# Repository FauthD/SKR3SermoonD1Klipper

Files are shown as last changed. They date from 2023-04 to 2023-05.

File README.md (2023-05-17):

# SKR3SermoonD1Klipper
Klipper settings for BTT SKR3 built into the Creality Sermoon D1

## Status
Printer works fine and I think not much will come anymore from my side.
The reason is that I switch to another board (MKS Monster8). It is not the fault of the SKR3 board which is a very fine board with very good documentation and a fair price.

However I want to add an auxilary feeder (extruder) that ensures the filament gets feed correctly into the direct extruder. Currently I sometimes have issues with material transport and get under extrusion. For that extra stepper motor it needs an extra driver, one too much for the SKR3. Yes, there is the Ext-M board that can extend the SKR3 with 3 more axes. I even created a mounting holder that can carry an EXT board. Unfortunatelly none of the stores I checked (many!) could deliver this board with reasonable delivery time. Since I can re-use the SKR3 in another project, I decided to go with a board with at least one more axis. The MKS Monster8 is small enough to fit easily underneath the fan. (The Octopus board is quite a bit wider).
Find my repo for the Monster8 here: https://github.com/FauthD/MksMonster8V2SermoonD1Klipper .

## Mechanics
Created an adapter to mount the SKR 3 since it does not fit to the mounting holes in the Sermnoon D1. Later I added some mounts for a big 120mm fan (because it was easier with a fan larger than the board). The fan runs with about 600 rmp and is barly audible.

Since I planed to add an extra stepper for a auxilary feeder, some space for the BTT Exp board was neccessary. Find the .stl and .scad files in directory SKR3-Adapter and below.

| No fan | 120mm fan | 120mm fan + ext board |
| :----: | :----: | :----: |
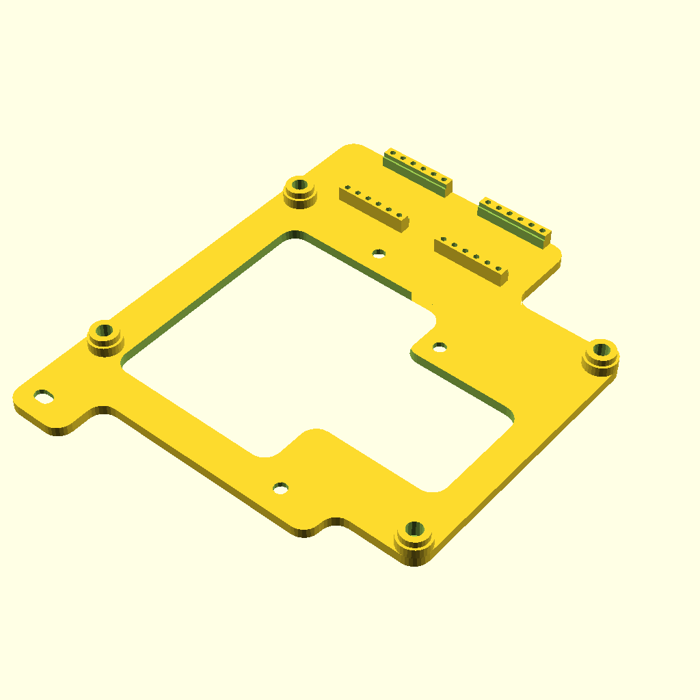
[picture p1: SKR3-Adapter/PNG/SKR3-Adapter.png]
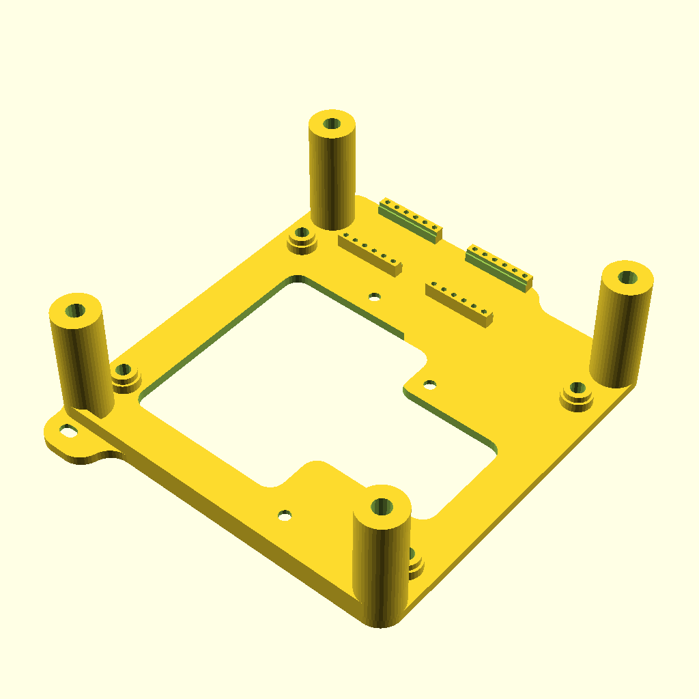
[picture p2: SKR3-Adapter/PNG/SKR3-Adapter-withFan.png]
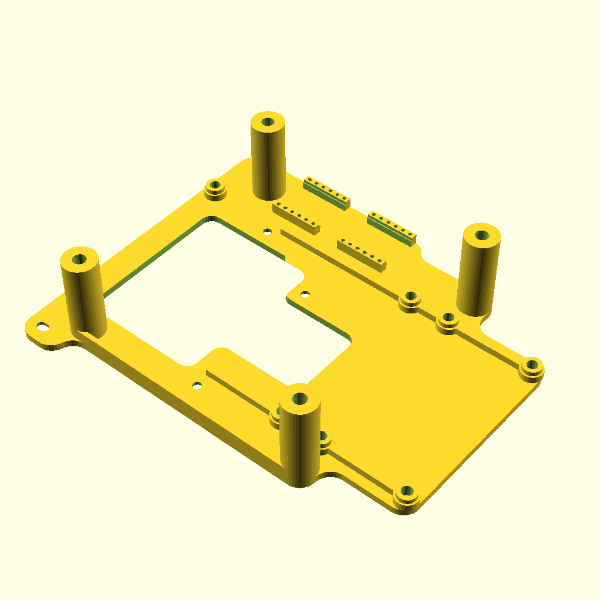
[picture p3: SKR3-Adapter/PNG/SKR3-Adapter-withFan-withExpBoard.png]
|  |  | 

Note: You either need to cut a hole onto the bottom sheet or replace it with some new bottom and larger feet. (Due to the board change I will not design a new bottom sheet for this board.)

Note2: The original mainboard fan does not transport much air, but makes quite some noise. So a slow turning 120mm fan running at 7V is much better.
The next source of noise is the fan in the power supply. I replaced that fan with a low noise 120mm fan running from 12V. Now it is barly audible and still produces a much better airflow. PSU stays cool even for long prints.
Both the 12V and the 7V are generated by cheap (0.7€+shipping) step down regulators. They are mounted onto the adapter.

Note3: We need heigher feet. Already printed some test feet with 28mm height (need 40mm screws - probably will increase by 5mm when I have that screws available).

Note4: I cannot check whether the original wires are long enough since I did buy the printer used and the wires are not original anymore.

### Rebuilding the .stl files
You need openscad installed.

On Linux, navigate into the directory SKR3-Adapter, open a cmd line and run make.

On Windows you also need some version of gmake installed. I do not use Windows anmore, so you are on your own.

### Photos:

| Adapter | Mainboard | Step down regulators | Total |
| :----: | :----: | :----: | :----: |
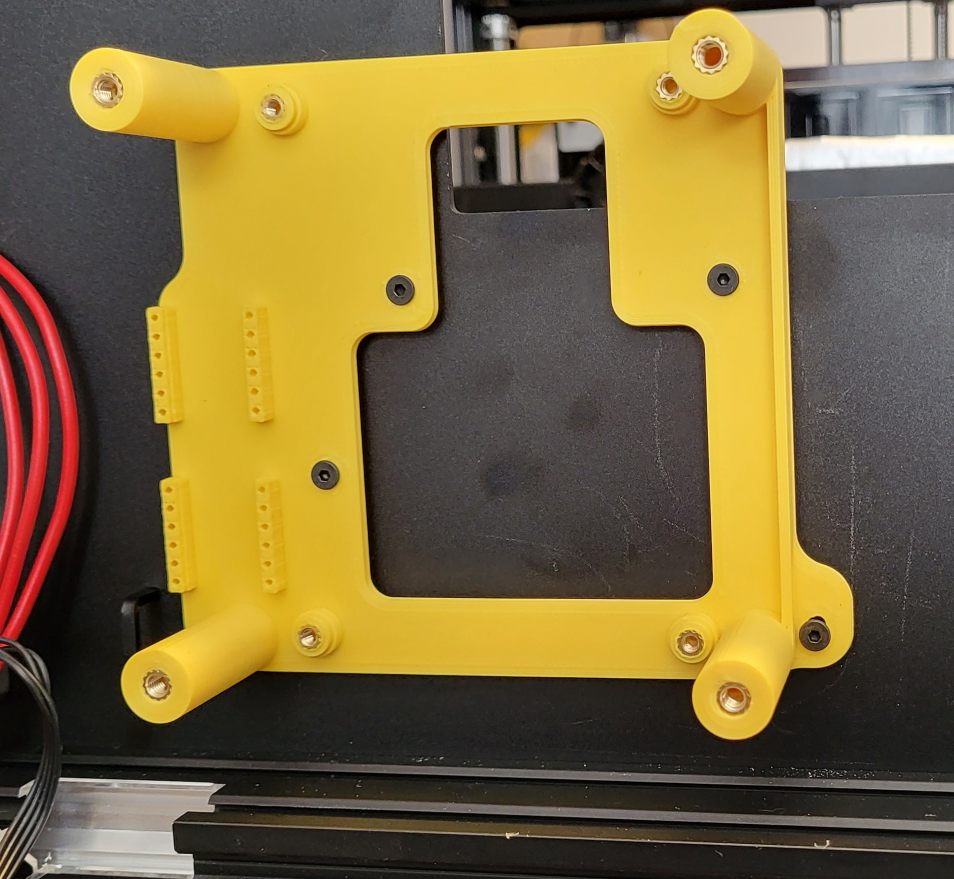
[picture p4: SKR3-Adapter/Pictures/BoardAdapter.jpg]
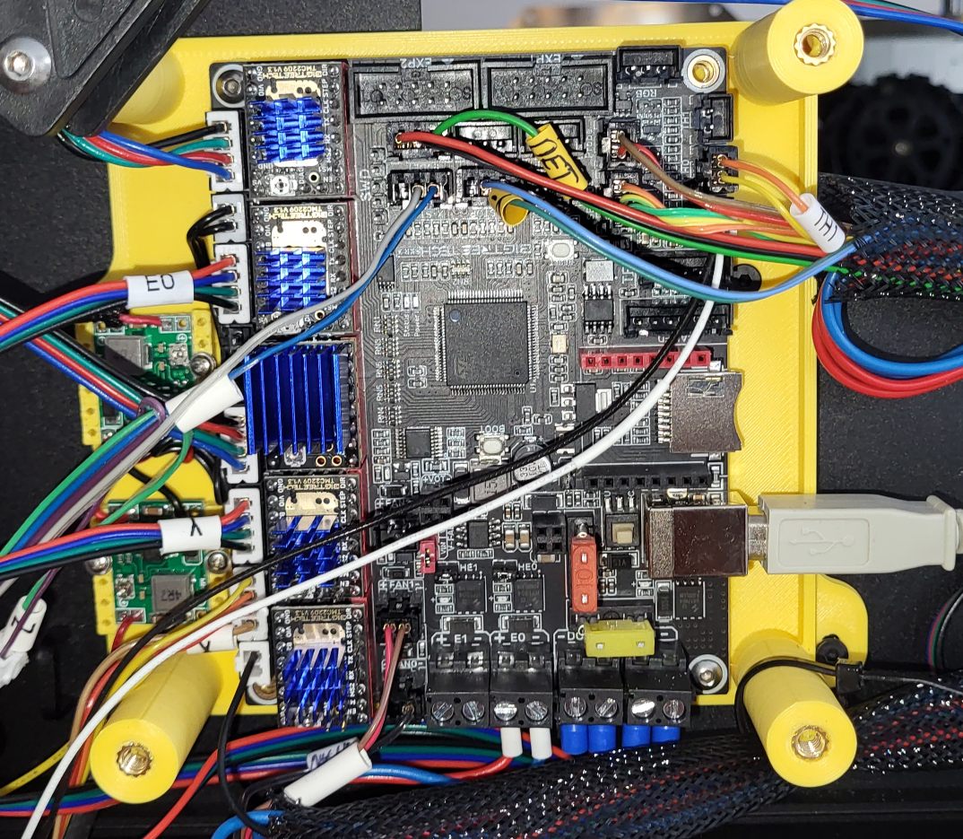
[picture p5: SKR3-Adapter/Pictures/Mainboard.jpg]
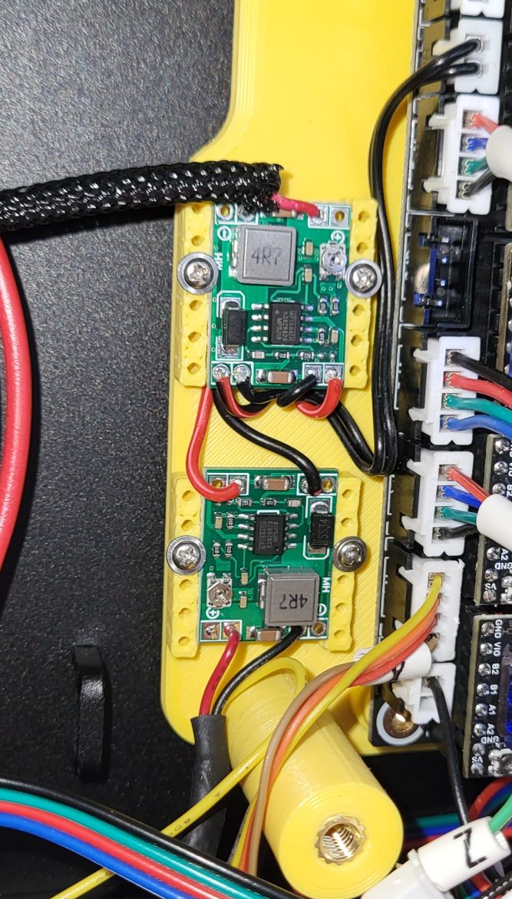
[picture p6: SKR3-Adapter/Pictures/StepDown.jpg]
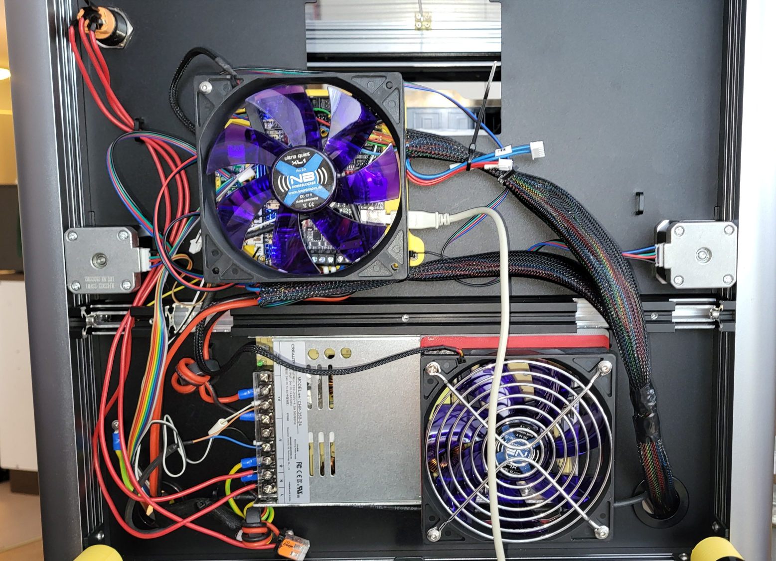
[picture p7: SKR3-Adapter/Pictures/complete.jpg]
|  |  |  |  |

## Klipper
Installed MainsaleOS on a RPi, created the firmware and flashed.
X and Y axis work including the limit switches.

CR Touch is working fine.
Even the Z-Tilt option works very nice.
Z Axis is much more silent (one reason I did all this, the original drivers for Z are very noisy).

X and Y axis have some resonances when they move fast. Turning stealthchop on reduced the resonances a lot.

Extruder works and is calibrated.

Bed mesh works (I am not happy with my bed yet).

A test with a LED RGB ring was succesful, but this is merly an example.

Note: I had issues with the Z axes (suddenly lots of noise, intermediatly running in wrong direction). To hunt this I added an extra SKR 3 E3 mini board for the Z Axes (Klipper is so flexible).

At the end it turned out that the (new) cables to the steppers are faulty and provided not always a good contact. After replacing these, all was fine.

Now I am back to the SKR 3 only, but the extra lines for the Mini 3E are still there as comments.

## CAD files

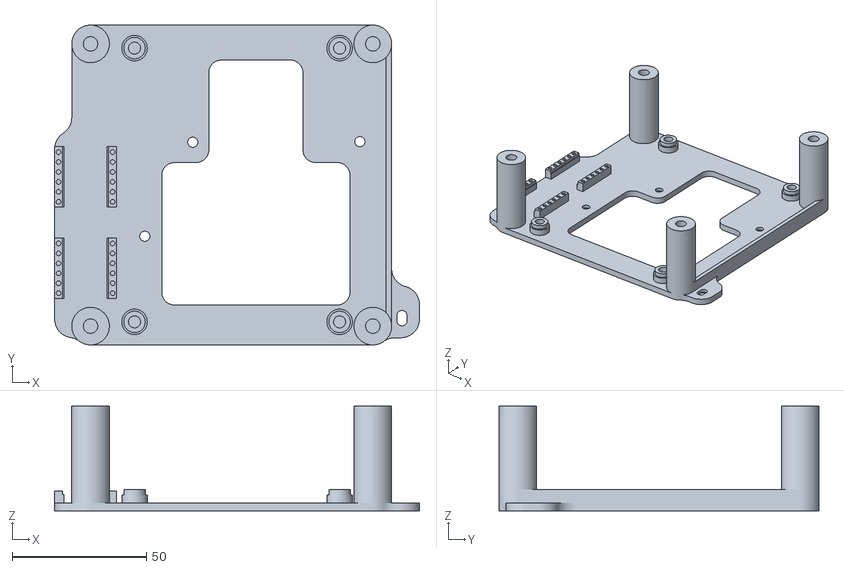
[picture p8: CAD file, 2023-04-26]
SKR3-Adapter/STL/SKR3-Adapter-withFan.stl
135.8 x 119.0 x 39.0

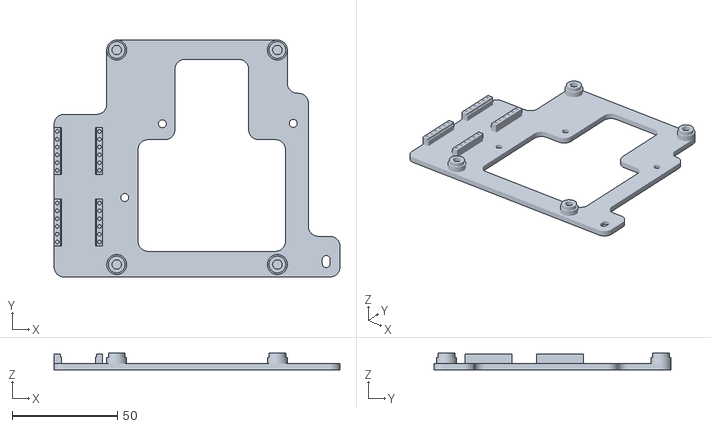
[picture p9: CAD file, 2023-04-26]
SKR3-Adapter/STL/SKR3-Adapter.stl
135.8 x 112.5 x 8.00

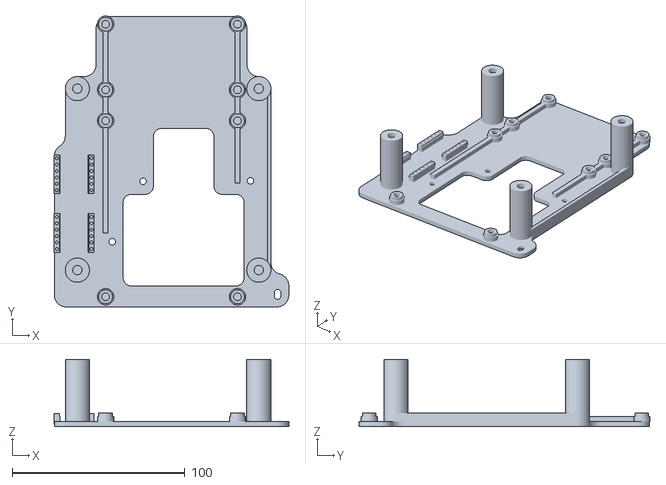
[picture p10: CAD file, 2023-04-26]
SKR3-Adapter/STL/SKR3-Adapter-withFan-withExpBoard.stl
135.8 x 168.4 x 39.0

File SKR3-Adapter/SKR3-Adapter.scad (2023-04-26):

// An adapter to mount the BTT SKR3 board into Creality mounting holes.
// Aimed for the Sermoon D1.
// The SKR3 is mounted 90° compared to the Creality board.
// This way the cables fit in lenght and there is enough room for the USB connector.
// For mounting you need 4 * M3 heat inserts (OD=5mm, l=4mm).
// I recommend to replace the original screws from the old board with ones with a flatter head.
//
// Copyright (C) 2023 Dieter Fauth
// This program is free software: you can redistribute it and/or modify it under the terms of the GNU General Public License as published by the Free Software Foundation, either version 3 of the License, or (at your option) any later version.
// This program is distributed in the hope that it will be useful, but WITHOUT ANY WARRANTY; without even the implied warranty of MERCHANTABILITY or FITNESS FOR A PARTICULAR PURPOSE. See the GNU General Public License for more details. You should have received a copy of the GNU General Public License along with this program. If not, see <http://www.gnu.org/licenses/>.
// Contact: dieter.fauth at web.de

/* [Print] */

PrintThis = "all"; // ["all", "mount"]

/* [Board Sizes] */
BoardLenght=109.7;
BoardWidth=84.3;

DrillLenght=101.85;
DrillWidth=76.3;
CrealityDrillDiameter=3.8;
// For M3 heat inserts use 4.5 else 2.5.
SkrDrillDiameter=4.5;
MountDiameter=9.5;

MountDistance=25;
MountHeight=5;
Thickness=3;

// Move SKR3 to the left
Offset_X=12;
// Move SKR3 to upper
Offset_Y=16;

/* [Options] */
UseFan=true;
FanDiameter=120;
FanScrewDistance=105;
// For M4 heat inserts use 5.4 else 3.5.
FanScrewDiameters=5.4;
FanMountingPostDiameter=14;
FanHeight=36;
// Move Fan to the left
FanOffset_X=2;

/* [EXP-Board] */
UseExpBoard=true;
ExpDistance=2;
ExpBoardLenght=46.0;
ExpDrillLenght=38.0;

/* [Hidden] */

module __Customizer_Limit__ () {}
    shown_by_customizer = false;

$fa = $preview ? 2 : 0.5;
$fs = $preview ? 1 : 0.5;

// If you enable the next line, the $fa and $fs are ignored.
// $fn = $preview ? 12 : 100;
Epsilon = 0.01;
epsilon = Epsilon;

/* Creality holes */
// These are relative to the lower left corner of the board.
// I took them from the BTT E3 Mini board.
// https://github.com/bigtreetech/BIGTREETECH-SKR-mini-E3/blob/master/hardware/BTT%20SKR%20MINI%20E3%20V3.0.1/Hardware/BTT%20E3%20SKR%20MINI%20V3.0.1_SIZE.pdf

E3Mini=[103.75, 70.25];

UnkownDifference=-1.0;  // one hole was not correct, empiric fix with a slotted hole

Drill1=[23.4,67.03, 0];
Drill2=[85.55, E3Mini.y-3.02, 0];
Drill3=[5.54, 32.05, 0];
Drill4=[37.34, 29.41, 0];
Drill5=[101.22, 2.56, 0];

Rounding=MountDiameter/2;

FanOffset_Y=UseExpBoard ? 17 : 0;
Enlarge=1.5;

///////////////////////////////////////////////////////////////////////////////
// Some helpers to round combined objects
module RoundConvex(r)
{
	offset(r = r)
	{
		offset(delta = -r)
		{
			children();
		}
	}
}

module RoundConcave(r)
{
	offset(r = -r)
	{
		offset(delta = r)
		{
			children();
		}
	}
}

module RoundThis(r)
{
	RoundConcave(r) RoundConvex(r) children();
}

// Can round combined 2D objects and make them 3D
module RoundExtrude(r, h)
{
	linear_extrude(height = h)
		RoundThis(r) children();
}

///////////////////////////////////////////////////////////////////////////////
// long hole
module SlottedHole(d, h, length)
{
   translate([0, 0, h/2])
      cube(size=[length, d, h+Epsilon], center=true);
      
   for(x=[-length/2,length/2])
   {
      translate([x, 0, h/2])
      {
         cylinder(d=d, h=h+Epsilon, center=true);
      }
   }
}

///////////////////////////////////////////////////////////////////////////////
// Helper for mounting step down boards with MP1584EN

module PcbMount(size, pcb)
{
   len=size.x;
   width=size.y+6;
   screw_dia=1.8;

   difference()
   {
      translate([0,0,size.z/2])
         cube([len,width, size.z], center=true);

      translate([0,0,size.z])
         cube([len+Epsilon,size.y, 2*pcb], center=true);

      translate([0,0,size.z/2])
         cube([len+Epsilon,size.y-1, size.z+Epsilon], center=true);

      for(n=[-1,1])
      {
         for(m=[-1:0.4:1])
         {
            translate([m*(len/2-2),n*(width/2-1.5),size.z/2])
               cylinder(d=screw_dia, h=20*size.z, center=true);
         }
      }
   }
}

module StepDown_MP1584EN()
{
   PcbMount(size=[22.5, 17.1, 6], pcb=1.4);
}

///////////////////////////////////////////////////////////////////////////////
// The Fan

module Fan(h=25)
{
   for(a=[45:90:360-Epsilon])
   {
      rotate([0,0,a])
         translate([FanScrewDistance/1.414, 0, 0])
         {
            difference()
            {
               cylinder(d=FanMountingPostDiameter, h=h, center=true);
               translate([0,0,h/2])
                  cylinder(d=FanScrewDiameters, h=h, center=true);
            }
         }
   }
}

///////////////////////////////////////////////////////////////////////////////
// The adapter

module CrealityHoles(d, h=5*Thickness)
{
   translate(Drill1)
      cylinder(d=d, h=h, center=true);
   translate(Drill2)
      cylinder(d=d, h=h, center=true);
   translate(Drill3)
      cylinder(d=d, h=h, center=true);
   translate(Drill4)
      cylinder(d=d, h=h, center=true);
   translate(Drill5)
      cylinder(d=d, h=h, center=true);
// fix some unknown difference in hole position
   translate([0,UnkownDifference,-h/2])
      translate(Drill5)
         rotate([0,0,90])
            SlottedHole(d=d, h=h, length=d/2);
}

module SKR3Holes()
{
      for(x=[-1,1])
      {
         for(y=[-1,1])
         {
            translate([x*DrillLenght/2, y*DrillWidth/2, 0])
               cylinder(d=SkrDrillDiameter, h=10*Thickness);
         }
      }
}

module ExpHoles()
{
      for(x=[-1,1])
      {
         for(y=[-1,1])
         {
            translate([x*ExpDrillLenght/2, y*DrillWidth/2, 0])
               cylinder(d=SkrDrillDiameter, h=10*Thickness);
         }
      }
}

module BasePlate()
{
   r=UseFan ? FanMountingPostDiameter/2 : Rounding;

   RoundExtrude(r, Thickness)
   {
      rotate([0,0,90])
         square([BoardLenght+Enlarge, BoardWidth+Enlarge], center=true);
      x=E3Mini.x+32;
      y=E3Mini.y+7;
      translate([-x/4, y/2-BoardLenght/2-2+FanOffset_Y/2])
         square([x/2, y+FanOffset_Y], center=true);
      translate([x/4-15, y/2-BoardLenght/2+8])
         square([x/2, y], center=true);
      translate([x/4, y/8-BoardLenght/2-2])
         square([x/2, y/4], center=true);
      
      if(UseExpBoard)
      {
         translate([0, BoardWidth+Enlarge])
            square([BoardWidth+2*Enlarge, ExpBoardLenght+2*Enlarge+ExpDistance], center=true);
      }

      if(UseFan)
      {
         size=FanDiameter-1;
         translate([-FanOffset_X, FanOffset_Y])
            square([size, size], center=true);
      }
   }
}

module CoolingHelper()
{
   RoundExtrude(Rounding, 10*Thickness)
   {
      translate([7, 4])
         square([35,85],center=true);

      translate([7, 20-DrillWidth/2])
         square([70,53],center=true);
   }
}

module BoardMounts(l,w)
   {
      for(x=[-1,1])
      {
         for(y=[-1,1])
         {
            translate([x*l/2, y*w/2, MountHeight/2+Thickness])
               cylinder(d=MountDiameter-1.5, h=MountHeight, center=true);
            translate([x*l/2, y*w/2, MountHeight/2+Thickness-1])
               cylinder(d=MountDiameter, h=MountHeight-2, center=true);
         }
      }
   }

module BoardHolder()
{
   BasePlate();
   rotate([0,0,90])
   {
      BoardMounts(DrillLenght, DrillWidth);
      if(UseExpBoard)
      {
         translate([BoardWidth+Enlarge+ExpDistance,0,0])
            BoardMounts(ExpDrillLenght, DrillWidth);
      }
   }
   if(UseExpBoard)
   {
      // enforcing a bit
      w=3;
      h=3;
      // l1=60;
      // translate([-0.7*l1+3, 0.7*l1+5, Thickness+h/2])
      //    rotate([0,0,35])
      //       cube([w, l1, h], center=true);
      l2=ExpBoardLenght+40+ExpDistance;
      translate([DrillWidth/2, l2/2+15, Thickness+h/2])
         cube([w, l2, h], center=true);
      l3=ExpBoardLenght+74+ExpDistance;
      translate([-DrillWidth/2, l3/2-14, Thickness+h/2])
         cube([w, l3, h], center=true);
   }
}

module Adapter()
{
   difference()
   {
      union()
      {
         BoardHolder();
         extra=4.5;
         for(n=[0,-1])
         {
            translate([-E3Mini.x/2-extra, n*34+3+FanOffset_Y, Thickness/2])
               rotate([0,0,90])
                  StepDown_MP1584EN();
         }
      }

      translate([0,0, Thickness])
         rotate([0,0,90])
         {
            SKR3Holes();
            translate([BoardWidth+Enlarge+ExpDistance,0,0])
               ExpHoles();
         }

      translate([-E3Mini.x/2+Offset_X, -E3Mini.y/2-Offset_Y, 0])
         CrealityHoles(CrealityDrillDiameter);
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

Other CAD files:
SKR3-Adapter/STL/withFan_withExpBoard.stl
SKR3-Adapter/STL/withFan.stl
SKR3-DrillingJig/SKR3-DrillingJig.scad

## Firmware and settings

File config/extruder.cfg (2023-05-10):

[extruder]
max_extrude_only_distance: 1000.0
step_pin: PD15
dir_pin: !PD14
enable_pin: !PC7
microsteps: 16
# after calibration
rotation_distance: 32.83
#rotation_distance: 33.500
nozzle_diameter: 0.400
filament_diameter: 1.750
heater_pin: PB3
sensor_type: EPCOS 100K B57560G104F
sensor_pin: PA2
control: pid
# after PID_CALIBRATE HEATER=extruder TARGET=200
pid_kp: 26.686
pid_ki: 1.534
pid_kd: 116.086
min_temp: 0
max_temp: 260
pressure_advance: 0.069

[tmc2209 extruder]
uart_pin: PC6
run_current: 0.600
diag_pin:

#[tmc2130 extruder1]
#cs_pin: PD12
#spi_software_miso_pin: PE15
#spi_software_mosi_pin: PE13
#spi_software_sclk_pin: PE14
#run_current: 0.800
#stealthchop_threshold: 999999
#diag1_pin: PA0

#extruder_stepper auxilary_feeder]
#extruder: extruder
#   The extruder this stepper is synchronized to. If this is set to an
#   empty string then the stepper will not be synchronized to an
#   extruder. This parameter must be provided.
#step_pin:
#dir_pin:
#enable_pin:
#microsteps:
#rotation_distance:
#   See the "stepper" section for the definition of the above
#   parameters.

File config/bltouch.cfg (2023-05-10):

# Before printing the PROBE_CALIBRATE command needs to be issued
# to run the probe calibration procedure, described at
# docs/Probe_Calibrate.md, to find the correct z_offset.

[safe_z_home]                           # enable for BLTouch
home_xy_position: 93, 143
speed: 100
z_hop: 10
z_hop_speed: 5

# bltouch must be directly in printer.cfg in order the SAVE_CONFIG can work

[bed_mesh]                              # enable for BLTouch
speed: 100
mesh_min: 50, 5
mesh_max: 270, 250
algorithm: bicubic
probe_count: 10, 10
fade_start: 1
fade_end: 10
fade_target: 0

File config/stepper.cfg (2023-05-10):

[stepper_x]
step_pin: PD4
dir_pin: PD3
enable_pin: !PD6
microsteps: 64
rotation_distance: 40
endstop_pin: ^PC1
position_min: -5
position_endstop: -5
position_max: 280
homing_speed: 50

[stepper_y]
step_pin: PA15
dir_pin: !PA8
enable_pin: !PD1
microsteps: 64
rotation_distance: 40
endstop_pin: ^PC3
position_min: -5
position_endstop: -5
position_max: 260
homing_speed: 50

[stepper_z]
step_pin: PE2
dir_pin: !PE3
enable_pin: !PE0
microsteps: 64
rotation_distance: 8
endstop_pin: probe:z_virtual_endstop
#endstop_pin: ^PC0
#position_endstop: 0.5
position_max: 300
homing_speed: 4
second_homing_speed: 1
homing_retract_dist: 2.0
position_min: -1

# This is marked as E1 stepper driver on SKR 3
[stepper_z1]
step_pin: PD11
dir_pin: !PD10
enable_pin: !PD13
microsteps: 64
rotation_distance: 8
endstop_pin: probe:z_virtual_endstop

########################################
# TMC2209 configuration
########################################

[tmc2209 stepper_x]
uart_pin: PD5
run_current: 0.800
diag_pin:
#stealthchop_threshold: 0
stealthchop_threshold: 999999

[tmc2209 stepper_y]
uart_pin: PD0
run_current: 0.800
diag_pin:
#stealthchop_threshold: 0
stealthchop_threshold: 999999

[tmc2209 stepper_z]
uart_pin: PE1
run_current: 0.8
diag_pin:
interpolate: False
#stealthchop_threshold: 0
stealthchop_threshold: 999999

[tmc2209 stepper_z1]
uart_pin: PD12
run_current: 0.8
diag_pin:
interpolate: False
#stealthchop_threshold: 0
stealthchop_threshold: 999999

########################################
# TMC2130 configuration
########################################

#[tmc2130 stepper_x]
#cs_pin: PD5
#spi_software_miso_pin: PE15
#spi_software_mosi_pin: PE13
#spi_software_sclk_pin: PE14
#run_current: 0.800
#stealthchop_threshold: 999999
#diag1_pin: PC1

#[tmc2130 stepper_y]
#cs_pin: PD0
#spi_software_miso_pin: PE15
#spi_software_mosi_pin: PE13
#spi_software_sclk_pin: PE14
#run_current: 0.800
#stealthchop_threshold: 999999
#diag1_pin: PC3

#[tmc2130 stepper_z]
#cs_pin: PE1
#spi_software_miso_pin: PE15
#spi_software_mosi_pin: PE13
#spi_software_sclk_pin: PE14
#run_current: 0.650
#stealthchop_threshold: 999999
#diag1_pin: PC0

#[tmc2130 extruder]
#cs_pin: PC6
#spi_software_miso_pin: PE15
#spi_software_mosi_pin: PE13
#spi_software_sclk_pin: PE14
#run_current: 0.800
#stealthchop_threshold: 999999
#diag1_pin: PC2

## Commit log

2023-04-12 First files (prrinter.cfg includes), untested an probably with errors and missing stuff.
    [bltouch.cfg, display.cfg, fans.cfg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]
2023-04-13 Add an adapter to mount the SKR 3 with 90°.
    [SKR3-Adapter.scad, SKR3-Adapter.stl, SKR3-DrillingJig.scad]
2023-04-13 Add image of mounting adapter.
2023-04-14 Move the SKR3 a bit to the left side (seen from bottom of the Sermoon with doors pointing up.
    [SKR3-Adapter.scad]
2023-04-14 Add a fan to the adapter. (Now with png and stl as well)
    [SKR3-Adapter.scad, SKR3-Adapter.stl, SKR3-Adapter_withFan.stl]
2023-04-14 Snapshot of klipper cfg.
    [bltouch.cfg, filament_sensor.cfg, heater_bed.cfg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]
2023-04-14 Z axis works (had wrong direction), CR-Touch works and homing of all 3 axis work (Z with CR-Touch.
    [bltouch.cfg, mainsail.cfg, stepper.cfg]
2023-04-15 Adjust BL-Touch settings to Sermmon D1.
    [bltouch.cfg]
2023-04-15 Adjust stepper values to Sermoon D1, Also add second stepper wich will be used by the z_tilt.
    [stepper.cfg]
2023-04-15 Add z-tilt settings (works perfect, I am so happy).
    [printer.cfg, z_tilt.cfg]
2023-04-25 Snapshot after rewire due to poor crimped connectors. Nozzle fan is now controlled by klipper (needs wiring mod), PID tunning for nozzle and bed, extruder now in extra file, added first steps with Le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
    [bed_screws.cfg, bltouch.cfg, extruder.cfg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]
2023-04-26 Adding a new flavour for the SKR3+BTT Exp board adapter. Adding makefile for the adapter openscad project. Move stl and png into subdir.
    [SKR3-Adapter.scad, SKR3-Adapter.stl, SKR3-Adapter_withFan.stl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]
2023-04-26 Renamed stl files, adjusted the readme.
    [SKR3-Adapter-withFan-withExpBoard.stl, SKR3-Adapter-withFan.stl, SKR3-Adapter.stl]
2023-04-27 Fine tune the bed screws.
    [bed_screws.cfg]
2023-04-27 Prepare beeper settings.
    [beeper.cfg]
2023-04-27 Add macros for start, end filament change.
    [filament_change.cfg, macros.cfg, start_end.cfg]
2023-04-27 Hunting an issue with the z axes. Using a second mcu for these axes.
    [mcu.cfg, mini-e3.cfg, printer.cfg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]
2023-05-01 Reconfigure Z axes back to the SKR 3, remove the Mini E3 board since I located the issue with my Z axes.
    [mcu.cfg, printer.cfg, stepper.cfg]
2023-05-09 Make mesh a bit larger.
    [bltouch.cfg]
2023-05-09 Calibrated pressure advance.
    [extruder.cfg]
2023-05-09 Check the z tild a bit more outside.
    [z_tilt.cfg]
2023-05-09 Add the prime line to the start macro, move the head out of the way in the end macro.
    [start_end.cfg]
2023-05-10 Mesh now fades out after 10 layers.
    [bltouch.cfg]
2023-05-10 Z axies now use 64 micro steps to make it much more silent.
    [stepper.cfg]
2023-05-10 Add example for auxilary_feeder (commented out).
    [extruder.cfg]
2023-05-11 Adding input shaper settings. Good improvement in X, a little in Y. The prints currently stands an a shaky desk, that for sure has some impact. Overall I am happy with the results.
    [input_shaper.cfg, printer.cfg, sermoon_d1.cfg]
2023-05-17 Latest mesh
    [printer.cfg]
2023-05-17 Reset max_accel back to 500 since it was way too much.
    [sermoon_d1.cfg]
2023-05-17 Optimize starrt and end macros.
    [start_end.cfg]
2023-05-17 Move klipper config in a subdir config.
    [bed_screws.cfg, beeper.cfg, bltouch.cfg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]
